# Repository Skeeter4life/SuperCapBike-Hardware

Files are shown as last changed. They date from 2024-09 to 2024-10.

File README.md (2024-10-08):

# This repository contains all the hardware needed for my supercapacitor bike.

## Main Features

  A 2 x ((500F @ 2.7V) x 6)  super-capacitor bank-based accumulator:
  
      1. Ability to provide high amounts of current instantaneously.
      
        This is well suited for my application where immediate throttle response is required. 
        The instant delivery of torque allows for aggressive accelerations when 
        changing from a low throttle position to full throttle.  

      2. Much more durable than a traditional battery.
        
        The super-capacitors can withstand many more full charge and discharge cycles
        without degradation. As such, they will undergo many charging cycles through 
        sources such as regenerative braking. Long service life is a priority.
      
      3. Quick charge times.

        Since super-capacitors have significantly less charge density than a battery, 
        it results in faster charging times. The primary intent is to only discharge 
        the super-capacitors to assist in climbing a hill.

  Series-Parallel Switching:

    This allows for a much more dynamic control over the power delivery from the super-capacitors. 
    To maximize runtime, the capacitors can be placed in parallel. 
    When the capacitors are getting low, or a large amount of power is required, 
    they can be switched into series. 

  More specific details can be found [here](https://www.desmos.com/calculator/0xlkaikos0).
    
## Current Components List

Ceramic Capacitors: 
- 0.1uF x 7 [^1], 
- 0.33uF x 2 [^2],
- 1uF x 3 [^3]

Electrolytic capacitors: 
- 10uF x 4 [^4]
  
Diodes:
- 1N4148 x 3 [^5], 
- 1N5819 x 4 [^6]

LEDs: 
- 5.0mm THT x2 [^7]

Fuse: 
- 0225002.MXP x1 [^8], 
- F4658-ND x 1 [^9]

Sockets & Pins: 
- 1x01 1.00mm Vertical Male Pin x 4 [^10], 
- 8 Dip 7.62mm Socket x 5 [^11],
- 16 Dip 7.62mm Socket x 1 [^12], 
- 28 Dip 7.62mm Socket x2 [^13] 

Barrel Jack: 
- PJ_002AH x 1 [^14]

Relays: 
- AWHSH105D00G x 2 [^15]

MOSFETS:
- IRFZ44N x 7 [^16], 
- GT065P06T x 1 [^17]

Resistors: 
- 220Ω, 10kΩ, 25kΩ, 55kΩ Resistor Kit: [^18]

Terminals: 
- 1988804 x 1 [^19], 
- 1988817 x 2 [^20], 
- 1190363 x2  [^21], 
- 1988862 x 3 [^22]

Microprocessors: 
- ATMEGA328P x 1 [^23]

Crystal Oscillator: 
- MXO45HST-3C-16M000000 x 1 [^24]

GPIO Expander: 
- MCP23017 x 1 [^25]

Button: 
- TS02-66-50-BK-160-LCR-D x 1 [^26]

MOSFET Gate Driver: 
- UCC37324P x 1 [^27] *OPTIONAL*

Darlington Transistors Array: 
- ULN2003 x 1 [^28]

Digital Potentiometers: 
- MCP4151 x 1 [^29]

Half Bridge Drivers: 
- IR2104 x 3 [^30]

Linear Regulators: 
-L7805 x1 [^31], 
- L78L33 x1 [^32]

Hall Effect Sensors: 
- TMAG5213AGQLPG x 3 [^33]

Switches: 
- 2057-SW-R-K1-A-ND x 1 [^34] 

Total raw components cost: **$ 113.95 CAD**

*Note: The prices here show the price for the exact number of the components listed. They were not entirely optimized. It would be significantly cheaper if components were bought in bulk*

## Schematic and PCB

### Schematic:  

  To reduce image congestion, please clone the repository and access the schematic on Kicad V8+.

### PCB:

<div align="center">

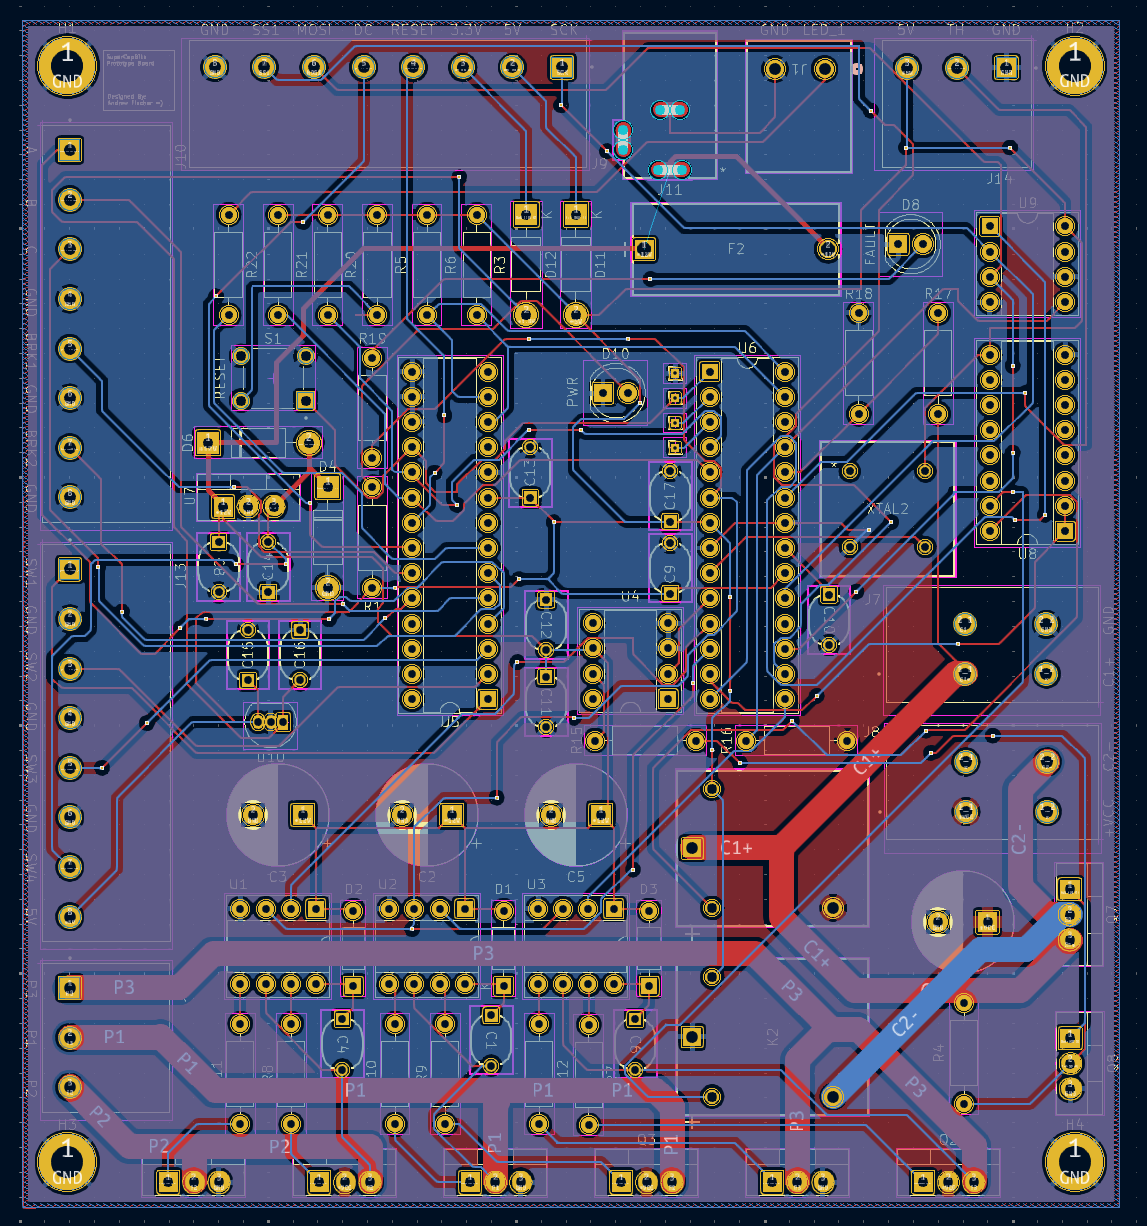
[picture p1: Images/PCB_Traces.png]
A photo of the PCB, traces visible
  
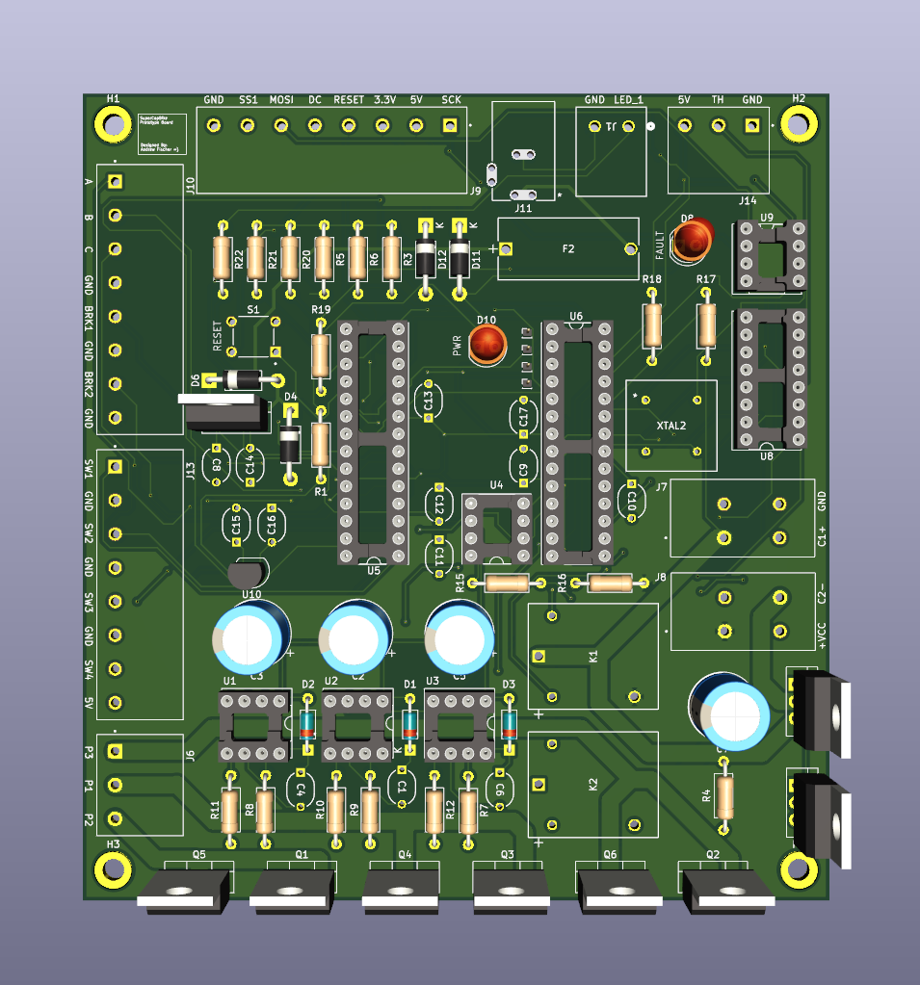
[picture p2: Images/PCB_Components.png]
A photo of the PCB, components clearly visible
  

</div>

## FAQ

  -Q: Why are you using only through-hole components?
  
  -A: Since some of these components are new to me, I wanted to be able to quickly set up and re-arrange components on a breadboard so I can fiddle and experiment with them.

  -Q: Why did you choose to design your PCB only with 2 layers?
  
  -A: As the current PCB is only a prototype, I did my best to mitigate EMI, however, I was not too overly concerned with it. I am considering isolating analog and digital ground. My main focus is to test my circuit design on a 2-layer 1oz copper pour PCB and see if any issues need addressing before proceeding to designing a more expensive 2oz copper 4-layer PCB.

  -Q: Why are you using a dedicated MOSFET driver IC to control Q8?
  
  -A: Admittedly, this component is completely optional and absolutely can be replaced with a simple current limiting resistor. Naturally, this does affect the switching speed of the transistor, and I want to maximize performance. I have the IC in hand, and the favourable transient response led me to implement it into my circuit.

  -Q: Why the relays?
  
  -A: I was able to simulate and build a circuit that switches two capacitors in series or parallel with only MOSFETS, however, the performance at low accumulator voltage was inadequate. Additionally, diodes were required to prevent reverse currents from connecting C2- to GND. As such, relays had significantly greater performance when switching the super-capacitors into parallel. I still kept Q7 and Q8 to switch the capacitors into series as a tribute to what I have learned from my experience with MOSFETs.

  -Q: Why did you choose the IRFZ44N?
  
  -A: The IRFZ44N is a widely used, affordable n-type MOSFET, as of which I have many on hand. I am well within the limitations of the drain current I_D, and drain source voltage V_DS. It has a favourable characteristic of only needing a V_GS of ~5.5V to supply 10A at a V_DS of ~ 0.3V. All transients were more than acceptable with the chosen MOSFET drivers for my application.  

  -Q: Why did you choose the GT065P06T?
  
  -A: I chose the GT065P06T primarily due to its outstanding R_DS of < 11mΩ at V_GS -4.5V for a p-type MOSFET and low gate charge. When the capacitors are in series, I want to minimize the power dissipated through that MOSFET without using PWM. 

## Technical Challenges

  As mentioned in the "Why the relays?" question, I was able to switch capacitors from parallel and series through MOSFETs alone, however, the overall performance was sub-optimal. The largest issue that occurred was with the MOSFETs I was using at the time (IRF530, n-type power MOSFET) when V_GS < ~4.5V, the MOSFET entered its cutoff region and the drain current I_D was significantly reduced. This is a problem because the entire system was designed to have a very low Norton resistance and 4.5V at a (to be verified exactly) ~5ohms is 900mA, which was experimentally found to be sufficient to drive the 500W motor. I replaced the IRF530s for IRFZ44Ns due to the nature of its V_DS(on) ~5.5V, however, it would still not solve the premise of the issue. Additionally, it was quite tricky to find a way to connect C2- to C1- (GND). C2- of course, is at a lower potential and current will flow through the body diode of the n-type MOSFET from GND to C2-. This can potentially be resolved through body diode cancellation with the addition of more MOSFETs, or the addition of Schottky diodes, however, this further increases cost and decreases the performance due to forward voltage drops. Thus, the hybrid solution of relays for connecting the super-capacitors in parallel and MOSFETs to connect them in series was implemented. 

## What I am Working on Now

I am currently installing the Hall effect sensors into the motor. The previous sensors were faulty and only outputted an average analog voltage of +3mV. An attempt was made to filter the signal from significant noise with the use of Schmitt triggers, however, this added significantly more complexity and cost. A replacement of the sensors was deemed to be the optimal solution.

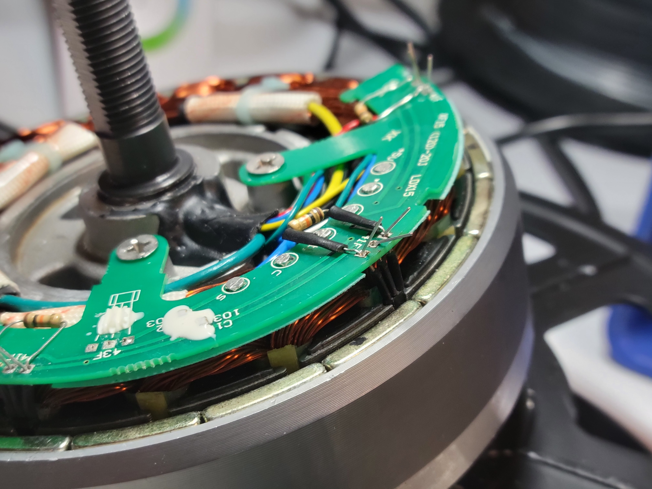
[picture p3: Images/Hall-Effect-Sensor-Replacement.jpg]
A photo of the the motor and replaced hall-effect sensors


## Sources

[^1]: https://www.digikey.ca/en/products/detail/kemet/C322C104M5U5TA/818107
[^2]: https://www.digikey.ca/en/products/detail/kemet/C330C334M5R5TA/6562403
[^3]: https://www.digikey.ca/en/products/detail/kemet/C330C105K5R5TA7301/3726162
[^4]: https://www.digikey.ca/en/products/detail/cornell-dubilier-knowles/106CKE400M/5410625
[^5]: https://www.digikey.ca/en/products/detail/onsemi/1N4148/458603
[^6]: https://www.digikey.ca/en/products/detail/stmicroelectronics/1N5819/1037326
[^7]: https://www.digikey.ca/en/products/detail/marktech-optoelectronics/MT4118-HR-A/4214622
[^8]: https://www.digikey.ca/en/products/detail/littelfuse-inc/02540101Z/553102
[^9]: https://www.digikey.ca/en/products/detail/littelfuse-inc/0225002-MXP/777781
[^10]: https://www.digikey.ca/en/products/detail/samtec-inc/TS-101-T-A/1105493
[^11]: https://www.digikey.ca/en/products/detail/te-connectivity-amp-connectors/1-2199298-2/5022039
[^12]: https://www.digikey.ca/en/products/detail/on-shore-technology-inc/ED16DT/4147596
[^13]: https://www.digikey.ca/en/products/detail/adam-tech/ICS-328-T/9832859
[^14]: https://www.digikey.ca/en/products/detail/same-sky/PJ-002AH/408446
[^15]: https://www.digikey.ca/en/products/detail/amphenol-anytek/AWHSH105D00G/16721986
[^16]: https://www.digikey.ca/en/products/detail/umw/IRFZ44N/24889964
[^17]: https://www.digikey.ca/en/products/detail/goford-semiconductor/GT065P06T/18088004
[^18]: https://www.digikey.ca/en/products/detail/sparkfun-electronics/COM-10969/14671649
[^19]: https://www.digikey.ca/en/products/detail/phoenix-contact/1988804/950892
[^20]: https://www.digikey.ca/en/products/detail/phoenix-contact/1988817/950893
[^21]: https://www.digikey.ca/en/products/detail/phoenix-contact/1190363/14680902
[^22]: https://www.digikey.ca/en/products/detail/phoenix-contact/1988862/950898
[^23]: https://www.digikey.ca/en/products/detail/microchip-technology/ATMEGA328P-PN/2357094
[^24]: https://www.digikey.ca/en/products/detail/cts-frequency-controls/MXO45HST-3C-16M000000/1801910
[^25]: https://www.digikey.ca/en/products/detail/microchip-technology/MCP23017-E-SP/894272
[^26]: https://www.digikey.ca/en/products/detail/same-sky-formerly-cui-devices/TS02-66-50-BK-160-LCR-D/15634352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
[^27]: https://www.digikey.ca/en/products/detail/texas-instruments/UCC37324P/571464
[^28]: https://www.digikey.ca/en/products/detail/stmicroelectronics/ULN2003A/599603
[^29]: https://www.digikey.ca/en/products/detail/microchip-technology/MCP4151-103E-P/1874217
[^30]: https://www.digikey.ca/en/products/detail/infineon-technologies/IR2104PBF/812198
[^31]: https://www.digikey.ca/en/products/detail/stmicroelectronics/L7805CV/585964
[^32]: https://www.digikey.ca/en/products/detail/stmicroelectronics/L78L33ABZ-AP/1663442
[^33]: https://www.digikey.ca/en/products/detail/texas-instruments/TMAG5213AGQLPG/22531584
[^34]: https://www.digikey.ca/en/products/detail/adam-tech/SW-R-K1-A/15284469

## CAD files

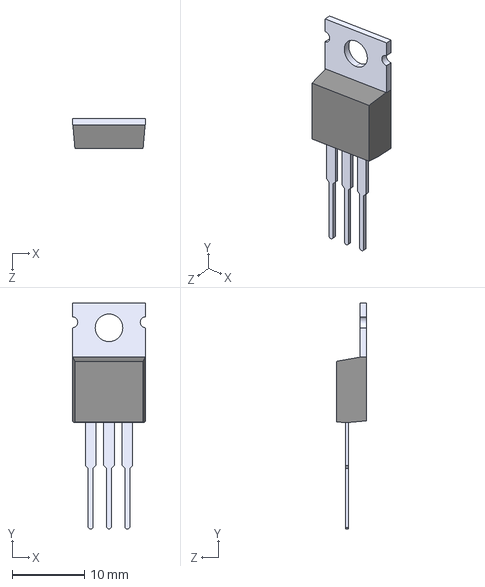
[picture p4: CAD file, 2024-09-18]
Libraries_Kicad/Footprints/IRFZ44N/IRFZ44N.step
10.2 x 31.2 x 4.19 mm

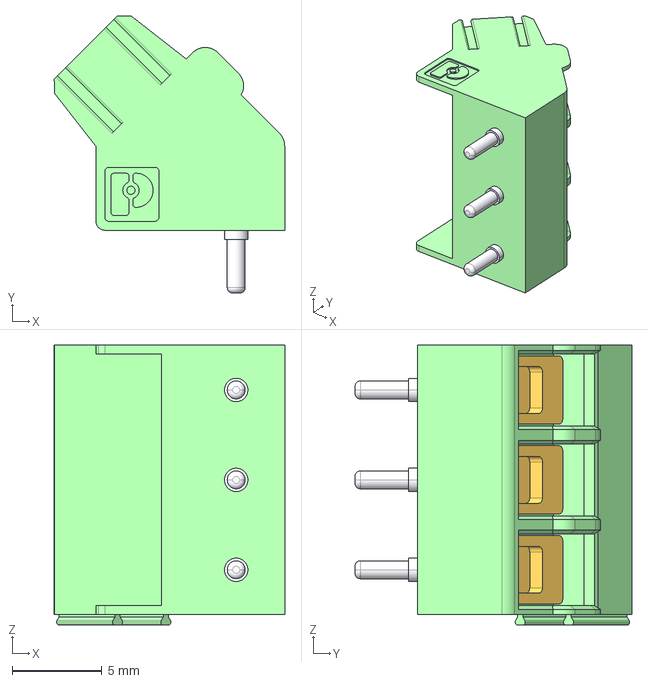
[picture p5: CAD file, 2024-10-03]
Libraries_Kicad/Footprints/Terminal_1988817/1988817.step
12.8 x 15.4 x 15.6 mm

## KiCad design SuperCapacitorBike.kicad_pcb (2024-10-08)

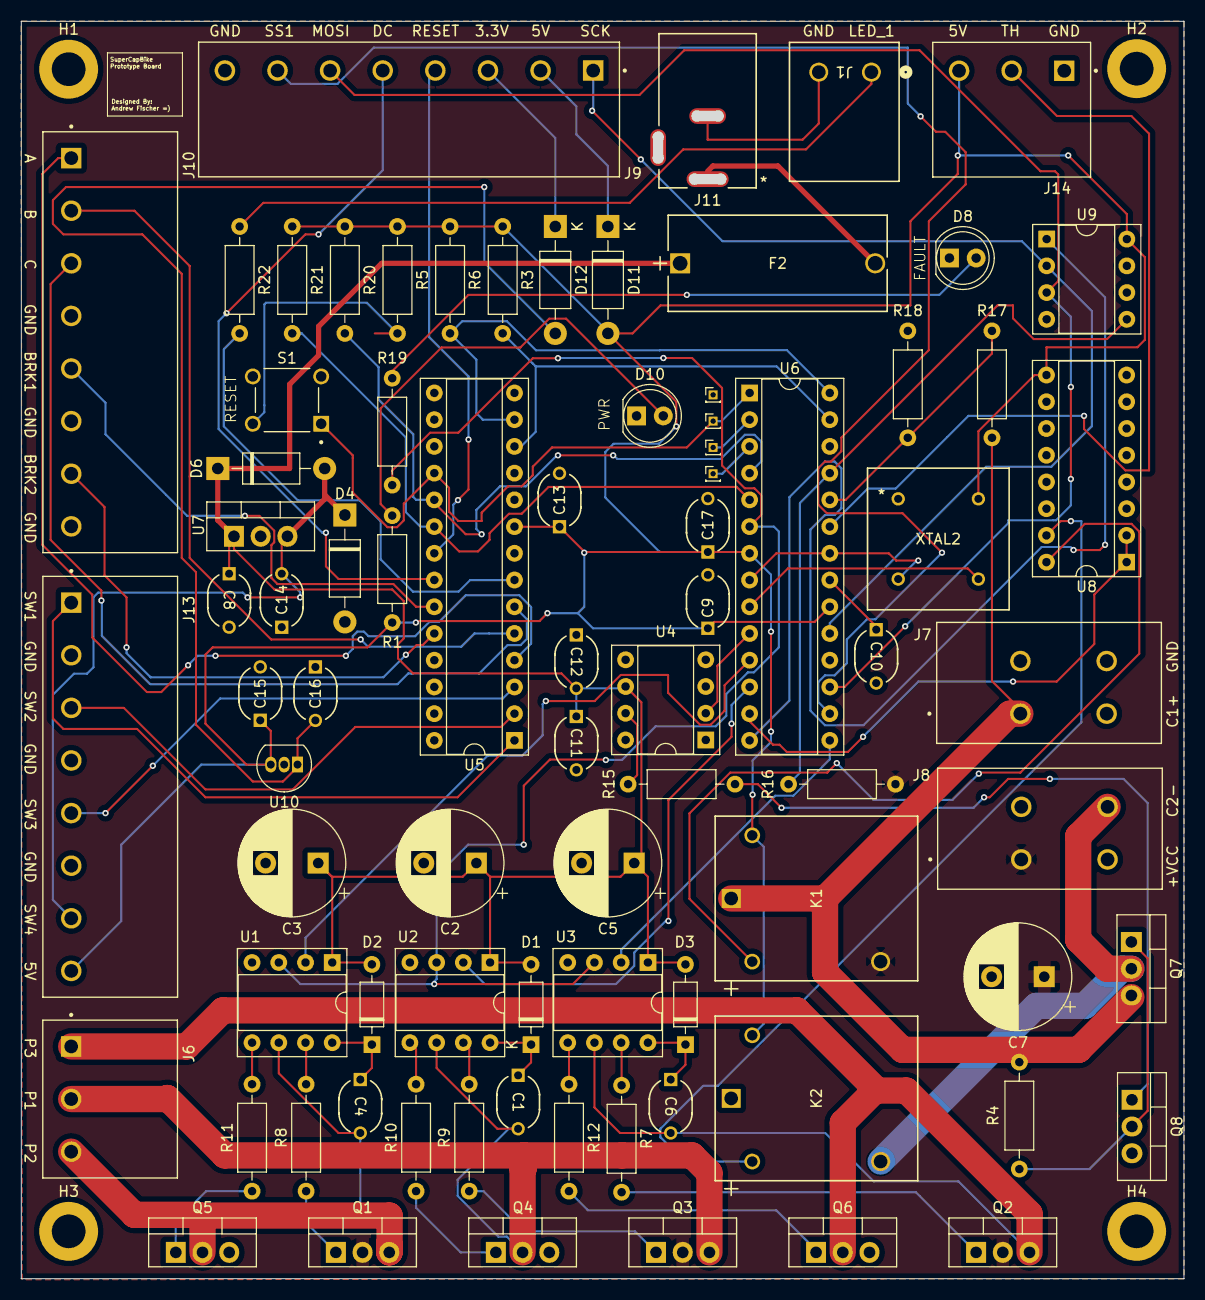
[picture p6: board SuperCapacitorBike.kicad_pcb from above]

Board: 2 copper layers, 110.5 x 119.5 mm, 85 parts (0 on the bottom side), 70 nets.

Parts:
C1, C4, C6: 1uF; Ceramic_Cap_5.08mm_Spacing
C2, C3, C5, C7: 10uF; CP_Radial_D10.0mm_P5.00mm
C8, C15: 0.33uF; Ceramic_Cap_5.08mm_Spacing
C9, C10, C11, C13, C14, C16, C17: 0.1uF; Ceramic_Cap_5.08mm_Spacing
C12: 1.0uF; Ceramic_Cap_5.08mm_Spacing
D1, D2, D3: 1N4148; D_DO-35_SOD27_P7.62mm_Horizontal
D4, D6, D11, D12: 1N5819; D_DO-41_SOD81_P10.16mm_Horizontal
D8: FAULT_LED; LED_D5.0mm
D10: PWR_LED; LED_D5.0mm
F2: 0225002.MXP; FUSE_254_PC_LTF
H1, H2, H3, H4: MountingHole_Pad; MountingHole_3.2mm_M3_DIN965_Pad
J1: 1988804; CONN_1988804
J2: GND; PinHeader_1x01_P1.00mm_Vertical
J3: RX; PinHeader_1x01_P1.00mm_Vertical
J4: TX; PinHeader_1x01_P1.00mm_Vertical
J5: RESET; PinHeader_1x01_P1.00mm_Vertical
J6, J14: 1988817; PHOENIX_1988817
J7, J8: 1190363; PHOENIX_1190363
J9, J10, J13: 1988862; PHOENIX_1988862
J11: Barrel_Jack_Switch; PJ-002AH_CUD
K1, K2: AWHSH105D00G; AWHSH1xxD00G_AMP
Q1, Q2, Q3, Q4, Q5, Q6, Q8: IRFZ44N; TO-220-3_Vertical
Q7: GT065P06T; TO-220-3_Vertical
R1, R19, R22: 220; R_Axial_DIN0207_L6.3mm_D2.5mm_P10.16mm_Horizontal
R3, R5, R6, R20, R21: 10k; R_Axial_DIN0207_L6.3mm_D2.5mm_P10.16mm_Horizontal
R4: 10kΩ; R_Axial_DIN0207_L6.3mm_D2.5mm_P10.16mm_Horizontal
R7, R8, R9, R10, R11, R12, R15: R_US; R_Axial_DIN0207_L6.3mm_D2.5mm_P10.16mm_Horizontal
R16: 20kΩ; R_Axial_DIN0207_L6.3mm_D2.5mm_P10.16mm_Horizontal
R17: 55kΩ; R_Axial_DIN0207_L6.3mm_D2.5mm_P10.16mm_Horizontal
R18: 25kΩ; R_Axial_DIN0207_L6.3mm_D2.5mm_P10.16mm_Horizontal
S1: TS02-66-50-BK-160-LCR-D; SW_TS02-66-50-BK-160-LCR-D
U1, U2, U3: IR2104; DIP-8_W7.62mm_Socket
U4: UCC37324P; DIP-8_W7.62mm_Socket
U5: MCP23017_SP; DIP-28_W7.62mm_Socket
U6: ATmega328-P; DIP-28_W7.62mm_Socket
U7: L7805; TO-220-3_Vertical
U8: ULN2003; DIP-16_W7.62mm_Socket
U9: MCP4151-xxxx-P; DIP-8_W7.62mm_Socket
U10: L78L33_TO92; TO-92_Inline
XTAL2: MXO45HST-3C-16M000000

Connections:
+3.3V: C16.2, D12.2 (A), U10.1 (VO)
+5V: C9.1, C13.1, C15.1, C17.1, D11.2 (A), J13.8, J14.3, K1.5, K2.5, R1.1, R3.1, R5.1, R6.1, R20.1, R21.1, U5.9 (VDD), U6.7 (VCC), U6.20 (AVCC), U8.9 (COM), U9.8 (V_{DD}), U10.3 (VI), XTAL2.8 (VCC)
+12V: C2.1, C3.1, C5.1, C8.1, C11.1, C12.2, D1.2 (A), D2.2 (A), D3.2 (A), D6.1 (K), F2.1, F2.2, J11.1, U1.1 (VCC), U2.1 (VCC), U3.1 (VCC), U4.6 (VDD), U7.1 (IN)
+VCC: C7.1, J8.1_1, K1.3, Q1.2 (D), Q2.2 (D), Q3.2 (D), R16.1
/Half bridge Circuit/HO_1: Q3.1 (G), R9.1
/Half bridge Circuit/HO_2: Q1.1 (G), R8.1
/Half bridge Circuit/HO_3: Q2.1 (G), R7.2
/Half bridge Circuit/LO_1: Q4.1 (G), R10.1
/Half bridge Circuit/LO_2: Q5.1 (G), R11.1
/Half bridge Circuit/LO_3: Q6.1 (G), R12.2
/Motor Controller/BRK1: J10.5, U5.23 (GPA2)
/Motor Controller/BRK2: J10.7, U5.24 (GPA3)
/Motor Controller/DC: J9.5, U5.22 (GPA1)
/Motor Controller/HALL_A: J10.1, U5.4 (GPB3)
/Motor Controller/HALL_B: J10.2, U5.5 (GPB4)
/Motor Controller/HALL_C: J10.3, U5.6 (GPB5)
/Motor Controller/INTA: R20.2, U5.19 (INTB), U6.4 (PD2)
/Motor Controller/INTB: R21.2, U5.20 (INTA), U6.5 (PD3)
/Motor Controller/LED_1: J1.1, R22.1
/Motor Controller/RELAYS: U6.13 (PD7), U8.1 (I1), U8.2 (I2)
/Motor Controller/RESET: J5.1, S1.1, U5.18 (~RESET), U6.1 (~RESET/PC6)
/Motor Controller/RESET_DISPLAY: J9.4, U5.21 (GPA0)
/Motor Controller/RX: J3.1, U6.2 (PD0)
/Motor Controller/SCL: R6.2, U5.13 (SDA), U6.28 (PC5)
/Motor Controller/SDA: R3.2, U5.12 (SCK), U6.27 (PC4)
/Motor Controller/SW_1: J13.1, U5.1 (GPB0)
/Motor Controller/SW_2: J13.3, U5.2 (GPB1)
/Motor Controller/SW_3: J13.5, U5.3 (GPB2)
/Motor Controller/SW_4: C14.2, D4.1 (K), D6.2 (A), J13.7, U7.3 (OUT)
/Motor Controller/TH_DATA: J14.2, U6.23 (PC0)
/Motor Controller/TX: J4.1, U6.3 (PD1)
/Motor Controller/XTAL1: U6.9 (XTAL1/PB6), XTAL2.5 (OUTPUT)
ADC_C1V: R17.2, R18.1, U6.24 (PC1)
ADC_C2V: R16.2, U6.25 (PC2), U9.5 (P0A)
C1+: J7.1_1, K1.1, Q7.3 (S), R4.1, R17.1
C2-: J8.2_2, K2.3, Q7.2 (D)
GND: C2.2, C3.2, C5.2, C7.2, C8.2, C9.2, C10.2, C11.2, C12.1, C13.2, C14.1, C15.2, C16.1, C17.2, D4.2 (A), D8.1 (K), D10.1 (K), H1.1, H2.1, H3.1, H4.1, J1.2, J2.1, J7.2_2, J9.8, J10.4, J10.6, J10.8, J11.2, J13.2, J13.4, J13.6, J14.1, K2.1, Q4.3 (S), Q5.3 (S), Q6.3 (S), Q8.3 (S), R18.2, S1.3, S1.4, U1.4 (COM), U2.4 (COM), U3.4 (COM), U4.3 (GND), U4.4 (INB), U5.10 (VSS), U5.15 (A0), U5.16 (A1), U5.17 (A2), U6.8 (GND), U6.22 (GND), U7.2 (GND), U8.8 (GND), U9.4 (V_{SS}), U9.6 (P0W), U10.2 (GND), XTAL2.4 (GND)
IN_1: U1.2 (IN), U6.12 (PD6)
IN_2: U2.2 (IN), U6.11 (PD5)
IN_3: U3.2 (IN), U6.15 (PB1)
MOSI: J9.6, U6.17 (PB3), U9.3 (SDI/SDO)
MOS_DRIVER: U4.2 (INA), U6.10 (XTAL2/PB7)
unnamed: C1.1, D1.1 (K), U1.8 (VB)
unnamed: C4.1, D2.1 (K), U2.8 (VB)
unnamed: C6.1, D3.1 (K), U3.8 (VB)
unnamed: D8.2 (A), R19.2
unnamed: D10.2 (A), R1.2
unnamed: D11.1 (K), J9.2
unnamed: D12.1 (K), J9.3
unnamed: Q7.1 (G), Q8.2 (D), R4.2
unnamed: Q8.1 (G), R15.2
unnamed: R5.2, S1.2
unnamed: R9.2, U1.7 (HO)
unnamed: R10.2, U1.5 (LO)
unnamed: R8.2, U2.7 (HO)
unnamed: R11.2, U2.5 (LO)
unnamed: R7.1, U3.7 (HO)
unnamed: R12.1, U3.5 (LO)
unnamed: R15.1, U4.7 (OUTA)
unnamed: R22.2, U5.7 (GPB6)
unnamed: C10.1, U6.21 (AREF)
P1: C1.2, J6.2, Q3.3 (S), Q4.2 (D), U1.6 (VS)
P2: C4.2, J6.3, Q1.3 (S), Q5.2 (D), U2.6 (VS)
P3: C6.2, J6.1, Q2.3 (S), Q6.2 (D), U3.6 (VS)
RELAY_1: K1.2, U8.16 (O1)
RELAY_2: K2.2, U8.15 (O2)
SCK: J9.1, U6.19 (PB5), U9.2 (SCK)
SD: R19.1, U1.3 (~SD), U2.3 (~SD), U3.3 (~SD), U6.6 (PD4)
SS1: J9.7, U6.16 (PB2)
SS2: U6.14 (PB0), U9.1 (~CS)

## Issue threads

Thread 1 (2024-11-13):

General PCB Notes

kyrel8silva, 2024-11-13:
Hey man! I just gave the schematic and PCB a quick look over. It looks pretty good! I'm impressed with how deep you have driven into the datasheets for a lot of these components. You must have learnt so much designing this board! It's crazy to think of how many little nuanced things get taken into account when designing something like this, especially something that needs to handle a lot of power. I've noted a few things below that may come up in some of your testing.

I'm not sure the xtal oscillator chosen will operate as intended. Normally for Atmega chips a xtal or ceramic oscillator is set between xtal1 and xtal 2. Buffer capacitors are also required for stability.
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

H-bridge drivers are only rated for 8V min. This means the drivers will only work for ~0.5 tau of the capacitor bank time constants.

Possibly need to add snubber or bi-directional TVS diodes to h-bridge outputs. Voltage spike by inductive load may cause damage to the circuit.

Some traces/vias need to be increased in size. Trace width calculators are handy for this sort of calculation.

Ground return paths can cause some interference on the analog measurements. Separation and suppression of the MOSFET's current path could help this.

Need to add bulk capacitance should be added to the following:
-uln2003 5V to gnd
-H-bridge FET's
-Power Rails
-I2C multiplexer

Just a thought also, use of an Arduino Mega may help simplify some things. The increased analog pins would remove the need for the i2c mux. Also, more flash and ram would be a nice help. Also with the Arduino Mega, it could be modified into a daughter board that plugs into the existing pin headers.

Let me know if you have any questions or want to go through a review sometime.

Skeeter4life, 2024-11-13:
Hello [kyrel8silva](https://github.com/kyrel8silva), thank you very much for the kind comments, and your well-documented insights. Below, I have responded to each inquiry with my reasoning/thought process:

1) I'm not sure the xtal oscillator chosen will operate as intended. Normally for Atmega chips a xtal or ceramic oscillator is set between xtal1 and xtal 2. Buffer capacitors are also required for stability.

    Totally valid, however, I have opted for a fully contained TTL HCMOS clock oscillator [[1]]. It reduced the total number of components, as I should be able to just put the output of it onto XTAL1. This as well as decreased the clock's susceptibility to noise. I have not been able to verify it is operating at 16MHz, however, ATmega328 datasheet references the need to change the CKSEL Fuses to use the internal 125kHz clock. I have not done this and I am able to run the ADC.

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

2) Possibly need to add snubber or bi-directional TVS diodes to h-bridge outputs. Voltage spike by inductive load may cause damage to the circuit.

    Honestly, I had not even heard of what a TVS diode was until you mentioned it (I have not even formally learned about diodes/transistors yet!).  I got pretty excited when I realized I could use that inductive spike in my half-bridge driver there for regenerative braking, and optimistically left the MOSFETs body diodes to do all the work. However, I definitely can see this being a problem, and potentially damaging the capacitors dielectric or generating an excess amount of heat in the motor. After you have mentioned it, a potential fix I am thinking about is adding two TVS diodes. The first TVS diode should have a breakdown voltage of 16V, and the other 32V, both carrying the excess back emf's current to ground. I would use a MOSFET to switch between the two TVS diodes if I am in series or parallel mode. I hope I am understanding the concept here correctly.

3) Some traces/vias need to be increased in size. Trace width calculators are handy for this sort of calculation.

    Ah, shoot, funnily enough, I did use a trace width calculator for the main traces such as the phases, the UCC37324P (even though I am seriously thinking now it does not need to be that wide), and the 12V fuse. I kept the standard trace widths and via sizes for everything else as they are all just carrying low current signals/serial data. I would definitely like to discuss this further with you. Also, it is worth re-iterating, that the final version of this board will have 2oz copper, not 1oz.

4) Ground return paths can cause some interference on the analog measurements. Separation and suppression of the MOSFET's current path could help this.

    I definitely can see how MOSFETs can interfere with the ADC on the ATmega. I don't have any real experience in EMI reduction/testing, but I did look into separating analog and digital grounds, if this is what you are referring to. It seems to be quite a controversial topic as some experts have said that it is entirely not worth it. If I recall correctly, one of the main issues with doing that is that you lose more by sacrificing the capacitive effect of having a uniform GND plane, which does more harm than good. It seems like a tricky thing to be able to do well, if at all. I would love to hear more about this.

5) Need to add bulk capacitance should be added to the following: uln2003 5V to gnd, H-bridge FET's, Power Rails, I2C multiplexer

    To be honest, the ULN2003 I find is the most abstract IC out of everything that is on there. I did not think it needed one as it is just a Darlington transistor array, and it is not preforming any sort of real logic. I am not super familiar/sure about adding capacitors to the MOSFET's. I do have one that connects VCC the common point for each phase of the half-bridge. In terms of the power rails, I thought that adding the capacitors specified by the datasheet for each linear regulator was sufficient. For the MCP23017, I sort of had the same logic for the ULN2003. I opted not to add any capacitors there because I did not see it as needing any sort of noise suppression or a constant flow of current. Generally speaking, its main job is just to pull the interrupt lines low when a switch is flicked or turn on an LED. I could be incorrect on this, and I understand a decoupling or bypass capacitor is always a good idea, I just did not think it needed one these cases.

6) Just a thought also, use of an Arduino Mega may help simplify some things. The increased analog pins would remove the need for the i2c mux. Also, more flash and ram would be a nice help. Also with the Arduino Mega, it could be modified into a daughter board that plugs into the existing pin headers.

    Oh absolutely, I even have a knock-off Arduino MEGA available to me, and that's initially the direction the project started. I was even considering using a Raspberry Pi 3. Using the chip from the MEGA would save some space and render the I/O expander as redundant, however, I am learning more by using these cool things.

I sincerely appreciate your time, and the effort you put into reviewing my design. I would love to go over it with you and discuss it greater detail.

[1]: https://www.digikey.ca/en/products/detail/cts-frequency-controls/MXO45HST-3C-16M000000/1801910

kyrel8silva, 2024-11-13:
0. H-bridge drivers are only rated for 8V min. This means the drivers will only work for ~0.5 tau of the capacitor bank time constants.
I didn't see you mention this issue when reviewing your comment. Honestly I don't have much experience running a motor driver off of supercaps like this. I don't know how these FET drivers will behave at lower voltages. I do think a driver like this is required for minimizing switching losses/heat, and it allows you to use all N-FET's which is super nice. This may just be something that needs to be tested in the real world before any conclusions can be derived.

1. Sorry for my ignorance. Very cool idea to implement the standalone Xtal oscillator! I haven't seen one used for the atmega chips but if they support it, it should be fine. The only limitation seems to be the requirement of high current drive. Some voltage stabilization may be required under loads for this oscillator to play nicely. But again, real world testing will tell you all you need to know.

2. Snubber or TVS diodes are super helpful when dealing with voltage spikes. Coming from the automotive world, they are my bread and butter. It is honestly crazy how many issues we have that are solved by simply slapping diodes everywhere. I'm glad you can see the potential of them! There are some nuanced characteristics for TVS diodes that can make implementation a bit more difficult. I'm more than happy to help with the TVS choices here if you want to chat about them sometime.
[https://www.ti.com/lit/an/slvae37/slvae37.pdf](url)

3. Trace widths are normally not an issue, until they are. You are right, for signals and serial data trace widths don't matter as much. There are a few scenarios in which the traces that are normally low current can face instances of higher current, causing voltage drops and weird logic errors when interacting in the digital realm. Trace widths become important when dealing with capacitors/inductors surge currents/voltages. 2oz copper is not usually needed. The larger surface area of wider traces can dissipate more heat. Relying on thicker copper to soak up the extra heat may just hide heat dissipation issues. Usually if I find I need 2oz copper, I start using parallel traces (top-bottom, or top-mid) and stitching them together with via's to increase the thermal conductivity and capacity. This is known as via stitching.
[https://www.globalwellpcba.com/pcb-via-stitching/](url)

4. Ground plane stuff is definitely not intuitive. I agree with the general consensus that it usually is not needed. For large current applications like this, it usually is a good idea. The current traveling along the ground plane can cause a difference in the "ground" voltage measured at the h-bridge drivers vs the other components. This difference becomes much greater when dealing with surge currents and high frequency noise that can be induced when driving inductive loads with FET's. The addition of bulk capacitance can assist in reducing the surge current traveling long distances across the PCB. Switching to a 4-layer PCB and having dedicated internal power/ground planes can be super helpful in reducing EMI and limiting the requirement of isolating the analog-digital grounds.

5.Bulk capacitance is a kind of safety catch to improve the stability of electronics during fast current switching. As the current draw of the electronics changes, the capacitor is able to stabilize the voltage seen by the device. Different capacitors can deliver current at different rates due to equivalent series resistance (ESR), plus a bunch of different stuff. Capacitors of different values (0.1uF, 1uF, 10uF, 100uF), also known as decades, are usually added in parallel in order to help filter different frequencies of noise.
You are correct in thinking that some of the devices that you are using do not draw much current, so they shouldn't need large capacitors. The issue is that these devices can switch voltages very quickly, (like nanosecond timescale) so they end up pulling the voltage low for tiny amounts of time, causing brown-out conditions.
The MCP23017 will also need to deal with the back EMF when the relay's coils are turned off. It looks like they should be able to handle it, but that initial voltage spike that occurs before the diode has completely turned on can be subdued with capacitors. Same goes for the FET outputs as well.
[https://www.ti.com/lit/an/slvaft0/slvaft0.pdf?ts=1731516352190](url)
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
Skeeter4life, 2024-11-19:
To recap, I plan on making a subsequent version, after I have sufficiently tested my current design. All issues you have mentioned will be credited. Please stay tuned!

Closed 2024-11-19.

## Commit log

2024-07-03 Version 1
    [SuperCapacitorBike.kicad_pcb, SuperCapacitorBike.kicad_sch]
2024-07-07 Improved filtering & Relay logic
    [SuperCapacitorBike.kicad_sch]
2024-07-12 Added circuit sim. file
2024-09-18 Complete redesign of the schematic
    [Accumulator.kicad_sch, Half_Bridge_Circuit_sch.kicad_sch, IRFZ44N.step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]
2024-09-28 Made progress on the PCB, and adressed small issues regarding the schematic
    [Accumulator.kicad_sch, Half_Bridge_Circuit_sch.kicad_sch, Motor_Controller_sch.kicad_sch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]
2024-10-03 Major design improvements to prototyping PCB
    [1988817.step, Accumulator.kicad_sch, Half_Bridge_Circuit_sch.kicad_sch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]
2024-10-08 Rebased 11 commits, Updated README, removed redundent sim file
    Added image files via upload
    For README
    Update README.md
    Update README.md
    Update README.md
    Update README.md
    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
2024-10-08 Added git ignore file
    [SuperCapacitorBike.kicad_pcb]
